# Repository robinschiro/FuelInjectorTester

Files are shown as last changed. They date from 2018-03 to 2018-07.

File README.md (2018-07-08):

# FuelInjectorTester
An Arduino-based device used to control fuel injectors for testing purposes.

# Background Information

- Injector injects onces per two turns of the engine

# Compiling the Code

- Get the Arduino IDE (https://www.arduino.cc/en/Main/OldSoftwareReleases)
- Unzip all dependencies (located in the 'Dependencies' folder) into the Arduino 'libraries' folder. The Arduino 'libraries' folder is located in the following locations (platform dependent):
	- (Windows) C:\Users\{User}\Documents\Arduino\libraries
	- (Unix) ~/sketchbook/libraries
- Open the 'FuelInjectorTester.ino' file using the Arduino IDE
- Click the button with a checkmark (top-left corner) to compile the code.

# Uploading Code to Arduino

# Requirements

- Support 4, 6, or 8 injectors
- LED lights that light up with fuel injectors
- Be able to adjust the following:
    - Number of injectors (4, 6 or 8)
    - Injection Time
    - RPM
    - Length of time the test will run
- Support different modes
    - Each mode should have configuration screen and running screen
    - Modes:
        - Testing
            - Injection Time: Range from 2 - 12 ms
            - RPM: range from 0 - 8000, increments of 100
        - Cleaning
            - Injection Time should range from 5 - 20 seconds, increments of 5
            - RPM: Range from 1 - 200 (use knob), increments of 1

# Problems
- If printing to LCD screen every frame, digital output to pins other than 13 does not work.
    - Possible Solution: Only drive the fuel injectors when in DRIVE_INJECTORS mode. In this mode, the UI is not updated. After exiting this mode, the UI will become responsive again.

# Express PCB Plus Grid Layout:
Grid: 2.5 mm
Snap: 0.25 mm

# Open questions
- Does simulating the firing order really matter?
	- Downside: Requires extra logic in the code

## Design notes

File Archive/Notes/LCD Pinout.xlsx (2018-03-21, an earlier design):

 | r5(sclk) | r3(d/c) | r1(sce) | vcc
red | yellow | blue | gray | black
brown | orange | green | violet | white
 | led | r4(dn) | r2(rst) | gnd

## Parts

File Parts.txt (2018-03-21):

Arduino Parts for Fuel Injector Project:

Vetco Electronics
15 day return policy

- New Arduino
- 2x Stackable header pins
    - 10 Pin Stacking Headers for Arduino (SKU: VUPN6552)
- Maybe a new shield that better fits my transistors
    - Need connections from the digital I/O pins to the shield holes
- Maybe a solution for my cable problem?
- Maybe a perf board?

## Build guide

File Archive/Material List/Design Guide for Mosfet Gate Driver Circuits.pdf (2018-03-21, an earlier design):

## Design And Application Guide For High Speed MOSFET Gate Drive Circuits

By Laszlo Balogh

ABSTRACT
The main purpose of this paper is to demonstrate a systematic approach to design high performance gate drive circuits for high speed switching applications. It is an informative collection of topics offering a “one-stop-shopping” to solve the most common design challenges. Thus it should be of interest to power electronics engineers at all levels of experience.
The most popular circuit solutions and their performance are analyzed, including the effect of parasitic components, transient and extreme operating conditions. The discussion builds from simple to more complex problems starting with an overview of MOSFET technology and switching operation. Design procedure for ground referenced and high side gate drive circuits, AC coupled and transformer isolated solutions are described in great details. A special chapter deals with the gate drive requirements of the MOSFETs in synchronous rectifier applications.
Several, step-by-step numerical design examples complement the paper.
INTRODUCTION
MOSFET – is an acronym for Metal Oxide
Semiconductor Field Effect Transistor and it is
the key component in high frequency, high efficiency switching applications across the electronics industry. It might be surprising, but FET technology was invented in 1930, some 20 years before the bipolar transistor. The first signal level FET transistors were built in the late 1950’s while power MOSFETs have been available from the mid 70’s. Today, millions of MOSFET transistors are integrated in modern electronic components, from microprocessors, through “discrete” power transistors.
The focus of this topic is the gate drive requirements of the power MOSFET in various switch mode power conversion applications. MOSFET TECHNOLOGY
The bipolar and the MOSFET transistors exploit the same operating principle. Fundamentally, both type of transistors are charge controlled devices which means that their output current is proportional to the charge established in the semiconductor by the control electrode. When these devices are used as switches, both must be driven from a low impedance source capable of sourcing and sinking sufficient current to provide for fast insertion and extraction of the controlling charge. From this point of view, the MOSFETs have to be driven just as “hard” during turn-on and turn-off as a bipolar transistor to achieve comparable switching speeds. Theoretically, the switching speeds of the bipolar and MOSFET devices are close to identical, determined by the time required for the charge carriers to travel across the semiconductor region. Typical values in power devices are approximately 20 to 200 picoseconds depending on the size of the device. The popularity and proliferation of MOSFET technology for digital and power applications is driven by two of their major advantages over the bipolar junction transistors. One of these benefits is the ease of use of the MOSFET devices in high frequency switching applications. The MOSFET transistors are simpler to drive because their control electrode is isolated from the current conducting silicon, therefore a continuous ON current is not required. Once the MOSFET transistors are turned-on, their drive current is practically zero. Also, the controlling charge and accordingly the storage time in the MOSFET transistors is greatly reduced. This basically eliminates the design trade-off between on state voltage drop – which is inversely proportional to excess control charge – and turn-off time. As a result, MOSFET technology promises to use much simpler and more efficient drive circuits with significant economic benefits compared to bipolar devices.
Furthermore, it is important to highlight especially for power applications, that MOSFETs have a resistive nature. The voltage drop across the drain source terminals of a MOSFET is a linear function of the current flowing in the semiconductor. This linear relationship is characterized by the RDS(on) of the MOSFET and known as the on-resistance. On-resistance is constant for a given gate-to-source voltage and temperature of the device. As opposed to the -2.2mV/°C temperature coefficient of a p-n junction, the MOSFETs exhibit a positive
temperature | coefficient | of | approximately
0.7%/°C to 1%/°C. This positive temperature coefficient of the MOSFET makes it an ideal candidate for parallel operation in higher power applications where using a single device would not be practical or possible. Due to the positive TC of the channel resistance, parallel connected MOSFETs tend to share the current evenly among themselves. This current sharing works automatically in MOSFETs since the positive TC acts as a slow negative feedback system. The device carrying a higher current will heat up more – don’t forget that the drain to source voltages are equal – and the higher temperature will increase its RDS(on) value. The increasing resistance will cause the current to decrease, therefore the temperature to drop. Eventually, an equilibrium is reached where the parallel connected devices carry similar current levels. Initial tolerance in RDS(on) values and different junction to ambient thermal resistances can cause significant – up to 30% – error in current distribution.
Device types
Almost all manufacturers have got their unique twist on how to manufacture the best power MOSFETs, but all of these devices on the market can be categorized into three basic device types. These are illustrated in Figure 1.

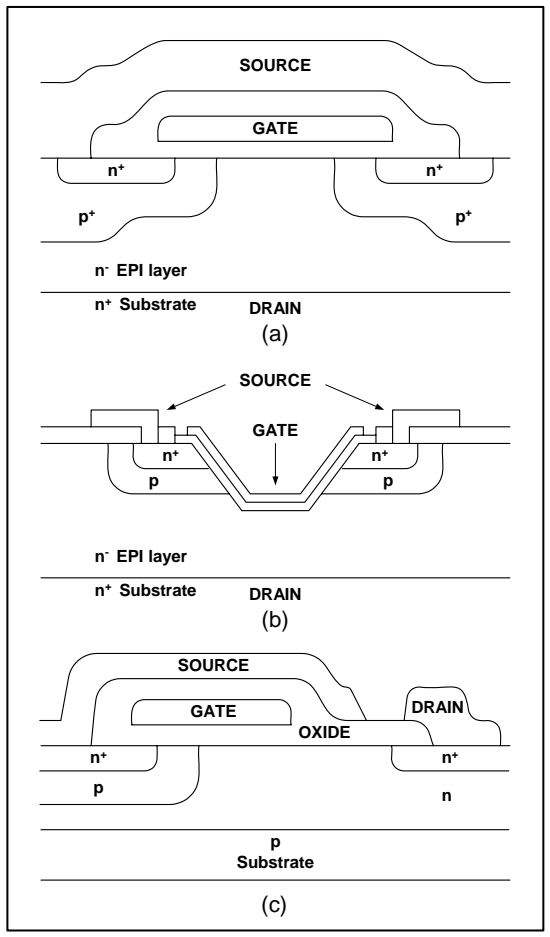
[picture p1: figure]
n⁺ Substrate; n⁻ EPI layer; GATE; SOURCE; DRAIN; Substrate; OXIDE

Figure 1. Power MOSFET device types
Double-diffused | MOS | transistors | were
introduced in the 1970’s for power applications and evolved continuously during the years. Using polycrystalline silicon gate structures and self-aligning processes, higher density integration and rapid reduction in capacitances became possible. The next significant advancement was offered by the V-groove or trench technology to further increase cell density in power MOSFET devices. The better performance and denser integration don’t come free however, as trench MOS devices are more difficult to manufacture.
The third device type to be mentioned here is the lateral power MOSFETs. This device type is constrained in voltage and current rating due to its inefficient utilization of the chip geometry. Nevertheless, they can provide significant benefits in low voltage applications, like in microprocessor power supplies or as synchronous rectifiers in isolated converters.

The lateral power MOSFETs have significantly lower capacitances, therefore they can switch much faster and they require much less gate drive power.
MOSFET Models
There are numerous models available to illustrate how the MOSFET works, nevertheless finding the right representation might be difficult. Most of the MOSFET manufacturers provide Spice and/or Saber models for their devices, but these models say very little about the application traps designers have to face in practice. They provide even fewer clues how to solve the most common design challenges.
A really useful MOSFET model which would describe all important properties of the device from an application point of view would be very complicated. On the other hand, very simple and meaningful models can be derived of the MOSFET transistor if we limit the applicability of the model to certain problem areas.
The first model in Figure 2 is based on the actual structure of the MOSFET device and can be used mainly for DC analysis. The MOSFET symbol in Figure 2a represents the channel resistance and the JFET corresponds to the resistance of the epitaxial layer. The length, thus the resistance of the epi layer is a function of the voltage rating of the device as high voltage MOSFETs require thicker epitaxial layer.
Figure 2b can be used very effectively to model the dv/dt induced breakdown characteristic of a MOSFET. It shows both main breakdown mechanisms, namely the dv/dt induced turn-on of the parasitic bipolar transistor - present in all power MOSFETs - and the dv/dt induced turn-on of the channel as a function of the gate
terminating | impedance. | Modern | power
MOSFETs are practically immune to dv/dt triggering of the parasitic npn transistor due to manufacturing improvements to reduce the resistance between the base and emitter regions. It must be mentioned also that the parasitic bipolar transistor plays another important role. Its base – collector junction is the famous body diode of the MOSFET.

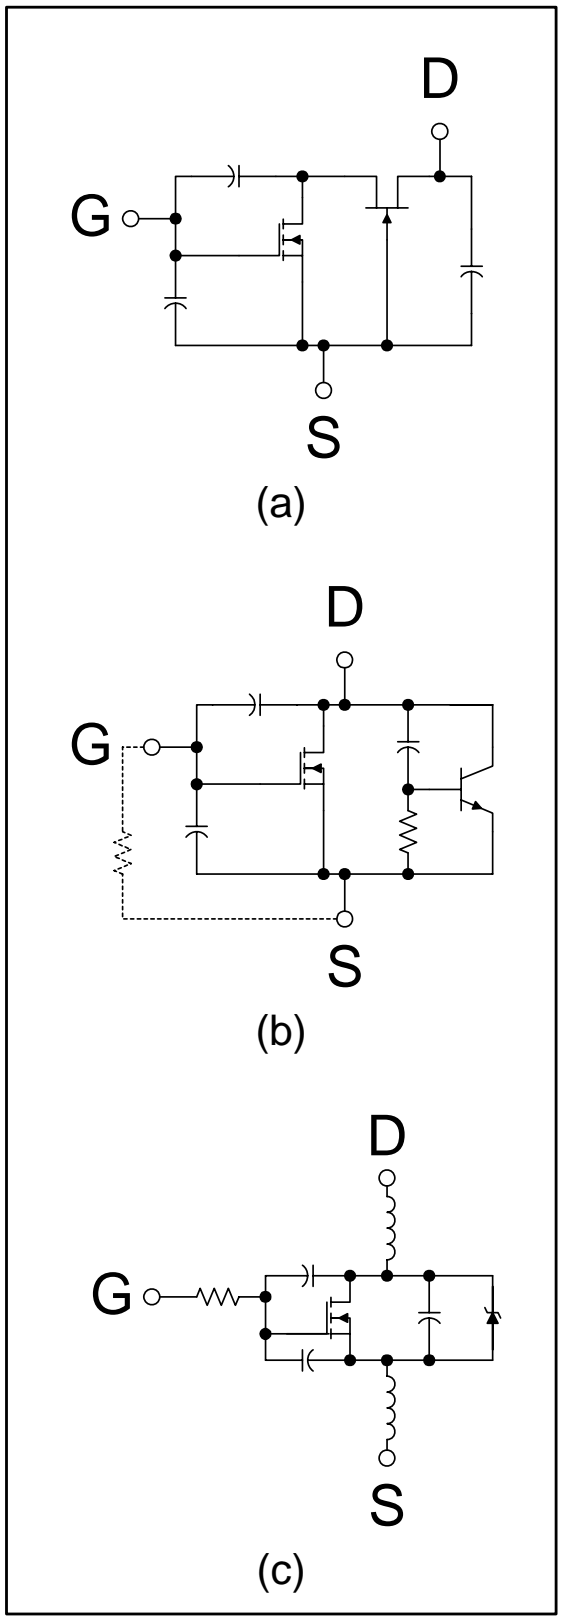
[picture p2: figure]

Figure 2. Power MOSFET models

Figure 2c is the switching model of the MOSFET. The most important parasitic components influencing switching performance are shown in this model. Their respective roles will be discussed in the next chapter which is dedicated to the switching procedure of the device.
MOSFET Critical Parameters
When switch mode operation of the MOSFET is considered, the goal is to switch between the lowest and highest resistance states of the device in the shortest possible time. Since the practical switching times of the MOSFETs (~10ns to 60ns) is at least two to three orders of magnitude longer than the theoretical switching time (~50ps to 200ps), it seems important to understand the discrepancy. Referring back to the MOSFET models in Figure 2, note that all models include three capacitors connected between the three terminals of the device. Ultimately, the switching performance of the MOSFET transistor is determined by how quickly the voltages can be changed across these capacitors.
Therefore, in high speed switching applications, the most important parameters are the parasitic capacitances of the device. Two of these
capacitors, the CGS | and CGD | capacitors
correspond to the actual geometry of the device while the CDS capacitor is the capacitance of the base collector diode of the parasitic bipolar transistor (body diode).
The CGS capacitor is formed by the overlap of the source and channel region by the gate electrode. Its value is defined by the actual geometry of the regions and stays constant (linear) under different operating conditions.
The CGD capacitor is the result of two effects. Part of it is the overlap of the JFET region and the gate electrode in addition to the capacitance of the depletion region which is non-linear. The equivalent CGD capacitance is a function of the drain source voltage of the device approximated by the following formula:

1 DS

GD,0
GD | 1 K | V
| C
C

+ ⋅ ≈

The CDS capacitor is also non-linear since it is the junction capacitance of the body diode. Its voltage dependence can be described as:

2 | DS

DS,0
DS | K | V

C
C ⋅ ≈

Unfortunately, non of the above mentioned capacitance values are defined directly in the transistor data sheets. Their values are given indirectly by the CISS, CRSS, and COSS capacitor values and must be calculated as:

DS | OSS | RSS
GS | ISS | RSS
GD | RSS
C | C | C
C | C | C
C | C
= | −
= | −

=

Further complication is caused by the CGD capacitor in switching applications because it is placed in the feedback path between the input and output of the device. Accordingly, its effective value in switching applications can be much larger depending on the drain source voltage of the MOSFET. This phenomenon is called the “Miller” effect and it can be expressed as:
( | ) CGD,eqv | 1 gfs RL | CGD = + ⋅ | ⋅

Since the CGD and CDS capacitors are voltage dependent, the data sheet numbers are valid only at the test conditions listed. The relevant average capacitances for a certain application have to be calculated based on the required charge to establish the actual voltage change across the capacitors. For most power MOSFETs the following approximations can be useful:

DS,off

DS,spec
OSS,ave | OSS,spec

DS,off

DS,spec
GD,ave | RSS,spec

V

V
C 2 C

V

V
C | 2 C
= ⋅ | ⋅
= ⋅ | ⋅

The next important parameter to mention is the gate mesh resistance, RG,I. This parasitic resistance describes the resistance associated by the gate signal distribution within the device. Its importance is very significant in high speed switching applications because it is in between the driver and the input capacitor of the device, directly impeding the switching times and the dv/dt immunity of the MOSFET. This effect is recognized in the industry, where real high speed devices like RF MOSFET transistors use metal gate electrodes instead of the higher resistance polysilicon gate mesh for gate signal distribution. The RG,I resistance is not specified in the data sheets, but in certain applications it can be a very important characteristic of the device. In the back of this paper, Appendix A4 shows a typical measurement setup to determine the internal gate resistor value with an impedance bridge. Obviously, the gate threshold voltage is also a critical characteristic. It is important to note that the data sheet VTH value is defined at 25°C and at a very low current, typically at 250μA. Therefore, it is not equal to the Miller plateau region of the commonly known gate switching waveform. Another rarely mentioned fact about VTH is its approximately –7mV/°C temperature coefficient. It has particular significance in gate drive circuits designed for logic level MOSFET where VTH is already low under the usual test conditions. Since MOSFETs usually operate at elevated temperatures, proper gate drive design must account for the lower VTH when turn-off time, and dv/dt immunity is calculated as shown in Appendix A and F.
The transconductance of the MOSFET is its small signal gain in the linear region of its operation. It is important to point out that every time the MOSFET is turned-on or turned-off, it must go through its linear operating mode where the current is determined by the gate-to-source voltage. The transconductance, gfs, is the small signal relationship between drain current and gate-to-source voltage:

GS

D
fs dV

dI
g =

Accordingly, the maximum current of the MOSFET in the linear region is given by:
( | ) D | VGS | Vth | gfs I = | − | ⋅

Rearranging this equation for VGS yields the approximate value of the Miller plateau as a function of the drain current.

fs

D
GS,Miller th
g

I V = V +

Other important parameters like the source inductance (LS) and drain inductance (LD) exhibit significant restrictions in switching performance. Typical LS and LD values are listed in the data sheets, and they are mainly dependant on the package type of the transistor. Their effects can be investigated together with the external parasitic components usually associated with layout and with accompanying external circuit elements like leakage inductance, a current sense resistor, etc.
For completeness, the external series gate resistor and the MOSFET driver’s output impedance must be mentioned as determining factors in high performance gate drive designs as they have a profound effect on switching speeds and consequently on switching losses.
SWITCHING APPLICATIONS
Now, that all the players are identified, let’s investigate the actual switching behavior of the MOSFET transistors. To gain a better understanding of the fundamental procedure, the parasitic inductances of the circuit will be neglected. Later their respective effects on the basic operation will be analyzed individually. Furthermore, the following descriptions relate to clamped inductive switching because most MOSFET transistors and high speed gate drive circuits used in switch mode power supplies work

Figure 3. Simplified clamped inductive switching model

The simplest model of clamped inductive switching is shown in Figure 3, where the DC current source represents the inductor. Its current can be considered constant during the short switching interval. The diode provides a path for the current during the off time of the MOSFET and clamps the drain terminal of the device to the output voltage symbolized by the battery. Turn-On procedure
The turn-on event of the MOSFET transistor can be divided into four intervals as depicted in Figure 4.

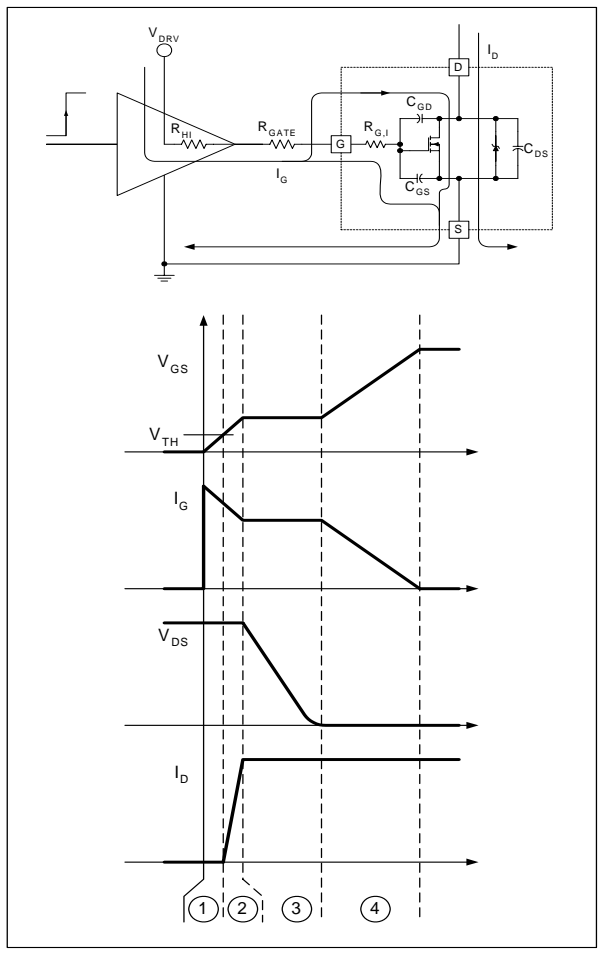
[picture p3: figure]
V DRV; RHI; RGATE; CGS; CDS; VGS; VTH

Figure 4. MOSFET turn-on time intervals In the first step the input capacitance of the device is charged from 0V to VTH. During this interval most of the gate current is charging the CGS capacitor. A small current is flowing through the CGD capacitor too. As the voltage increases at the gate terminal and the CGD capacitor’s voltage has to be slightly reduced.

This period is called the turn-on delay, because both the drain current and the drain voltage of the device remain unchanged.
Once the gate is charged to the threshold level, the MOSFET is ready to carry current. In the second interval the gate is rising from VTH to the Miller plateau level, VGS,Miller. This is the linear operation of the device when current is proportional to the gate voltage. On the gate side, current is flowing into the CGS and CGD capacitors just like in the first time interval and the VGS voltage is increasing. On the output side of the device, the drain current is increasing, while the drain-to-source voltage stays at the previous level (VDS,OFF). This can be understood looking at the schematic in Figure 3. Until all the current is transferred into the MOSFET and the diode is turned-off completely to be able to block reverse voltage across its pn junction, the drain voltage must stay at the output voltage level. Entering into the third period of the turn-on procedure the gate is already charged to the sufficient voltage (VGS,Miller) to carry the entire load current and the rectifier diode is turned off. That now allows the drain voltage to fall. While the drain voltage falls across the device, the gate-to-source voltage stays steady. This is the Miller plateau region in the gate voltage waveform. All the gate current available from the driver is diverted to discharge the CGD capacitor to facilitate the rapid voltage change across the drain-to-source terminals. The drain current of the device stays constant since it is now limited by the external circuitry, i.e. the DC current source.
The last step of the turn-on is to fully enhance the conducting channel of the MOSFET by applying a higher gate drive voltage. The final amplitude of VGS determines the ultimate on-resistance of the device during its on-time. Therefore, in this fourth interval, VGS is increased from VGS,Miller to its final value, VDRV. This is accomplished by charging the CGS and CGD capacitors, thus gate current is now split between the two components. While these capacitors are being charged, the drain current is still constant, and the drain-to-source voltage is slightly decreasing as the on-resistance of the device is being reduced.

Turn-Off procedure
The description of the turn-off procedure for the MOSFET transistor is basically back tracking the turn-on steps from the previous section. Start with VGS being equal to VDRV and the current in the device is the full load current represented by IDC in Figure 3. The drain-to-source voltage is being defined by IDC and the RDS(on) of the MOSFET. The four turn-off steps are shown in Figure 5. for completeness.

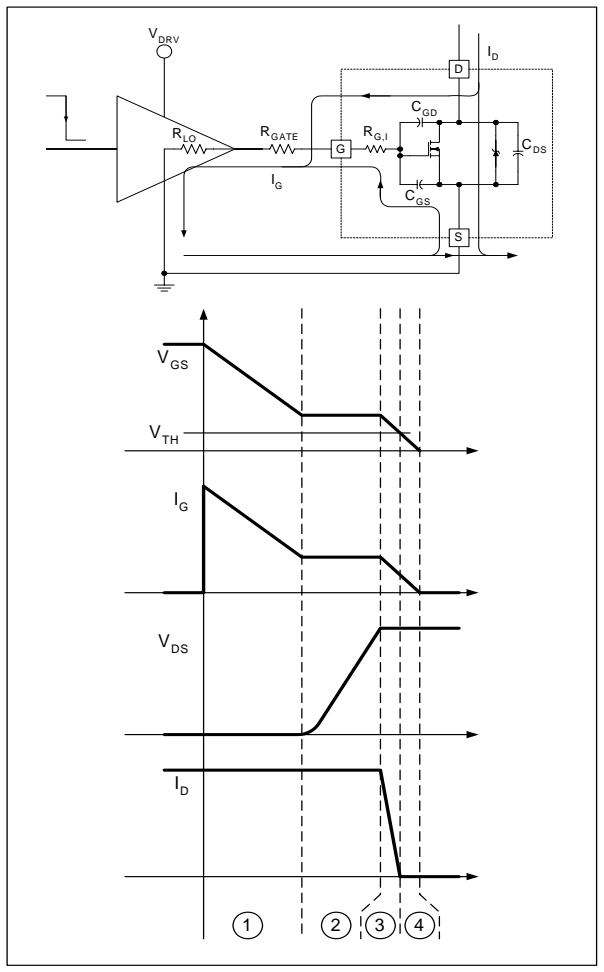
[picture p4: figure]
VDRV; RLO; RGATE; CGD; CGS; CDS; VDS; VGS; VTH

Figure 5. MOSFET turn-off time intervals The first time interval is the turn-off delay which is required to discharge the CISS capacitance from its initial value to the Miller plateau level. During this time the gate current is supplied by the CISS capacitor itself and it is flowing through the CGS and CGD capacitors of the MOSFET. The drain voltage of the device is slightly increasing as the overdrive voltage is diminishing. The current in the drain is unchanged.

In the second period, the drain-to-source voltage of the MOSFET rises from ID⋅RDS(on) to the final VDS(off) level, where it is clamped to the output voltage by the rectifier diode according to the simplified schematic of Figure 3. During this time period – which corresponds to the Miller plateau in the gate voltage waveform - the gate current is strictly the charging current of the CGD capacitor because the gate-to-source voltage is constant. This current is provided by the bypass capacitor of the power stage and it is subtracted from the drain current. The total drain current still equals the load current, i.e. the inductor current represented by the DC current source in Figure 3.
The beginning of the third time interval is signified by the turn-on of the diode, thus providing an alternative route to the load current. The gate voltage resumes falling from VGS,Miller to VTH. The majority of the gate current is coming out of the CGS capacitor, because the CGD capacitor is virtually fully charged from the previous time interval. The MOSFET is in linear operation and the declining gate-to-source voltage causes the drain current to decrease and reach near zero by the end of this interval. Meanwhile the drain voltage is steady at VDS(off) due to the forward biased rectifier diode.
The last step of the turn-off procedure is to fully discharge the input capacitors of the device. VGS is further reduced until it reaches 0V. The bigger portion of the gate current, similarly to the third turn-off time interval, supplied by the CGS capacitor. The drain current and the drain voltage in the device are unchanged.
Summarizing the results, it can be concluded that the MOSFET transistor can be switched between its highest and lowest impedance states (either turn-on or turn-off) in four time intervals. The lengths of all four time intervals are a function of the parasitic capacitance values, the required voltage change across them and the available gate drive current. This emphasizes the importance of the proper component selection and optimum gate drive design for high speed, high frequency switching applications.

Characteristic numbers for turn-on, turn-off delays, rise and fall times of the MOSFET switching waveforms are listed in the transistor data sheets. Unfortunately, these numbers correspond to the specific test conditions and to resistive load, making the comparison of different
manufacturers’ | products | difficult. | Also,
switching performance in practical applications with clamped inductive load is significantly different from the numbers given in the data sheets.
Power losses
The switching action in the MOSFET transistor in power applications will result in some unavoidable losses, which can be divided into two categories.
The simpler of the two loss mechanisms is the gate drive loss of the device. As described before, turning-on or off the MOSFET involves charging or discharging the CISS capacitor. When the voltage across a capacitor is changing, a certain amount of charge has to be transferred. The amount of charge required to change the gate voltage between 0V and the actual gate drive voltage VDRV, is characterized by the typical gate charge vs. gate-to-source voltage curve in the MOSFET datasheet. An example is shown in

# Figure 6. Vgs, Gate⁻to⁻Source Voltage ⁽V⁾

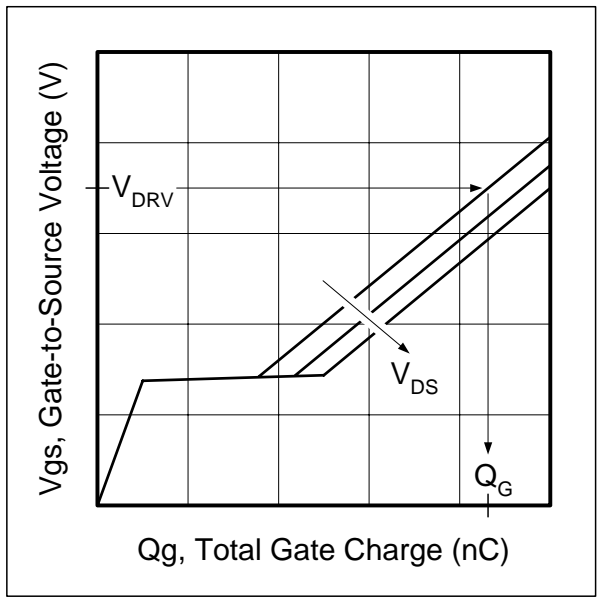
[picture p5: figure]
Qg, Total Gate Charge (nC); VDS; VDRV

Figure 6. Typical gate charge vs. gate-to-source voltage

This graph gives a relatively accurate worst case estimate of the gate charge as a function of the gate drive voltage. The parameter used to generate the individual curves is the drain-to-source off state voltage of the device. VDS(off) influences the Miller charge – the area below the flat portion of the curves – thus also, the total gate charge required in a switching cycle. Once the total gate charge is obtained from Figure 6, the gate charge losses can be calculated as:

GATE | DRV | G | DRV P | = V | ⋅Q ⋅f
where VDRV is the amplitude of the gate drive waveform and fDRV is the gate drive frequency – which is in most cases equal to the switching frequency. It is interesting to notice that the QG⋅fDRV term in the previous equation gives the average bias current required to drive the gate. The power lost to drive the gate of the MOSFET transistor is dissipated in the gate drive circuitry. Referring back to Figures 4 and 5, the dissipating components can be identified as the combination of the series ohmic impedances in the gate drive path. In every switching cycle the required gate charge has to pass through the driver output impedances, the external gate resistor, and the internal gate mesh resistance. As it turns out, the power dissipation is independent of how quickly the charge is delivered through the resistors. Using the resistor designators from Figures 4 and 5, the driver power dissipation can be expressed as:
DRV | DRV,ON | DRV,OFF
LO | GATE | G,I
LO | DRV | G | DRV
DRV,OFF
HI | GATE | | G,I
HI | DRV | G | DRV
DRV,ON
P | P | P
R | R | R
R | V | Q f
2

1 P

R | R | R
R | V | Q f
2

1 P

= | +
+ | +
⋅ | ⋅ | ⋅ = ⋅
+ | +
⋅ | ⋅ | ⋅ = ⋅

In the above equations, the gate drive circuit is represented by a resistive output impedance and this assumption is valid for MOS based gate drivers. When bipolar transistors are utilized in the gate drive circuit, the output impedance becomes non-linear and the equations do not yield the correct answers. It is safe to assume that with low value gate resistors (<5Ω) most gate drive losses are dissipated in the driver. If RGATE is sufficiently large to limit IG below the output current capability of the bipolar driver, the majority of the gate drive power loss is then dissipated in RGATE.
In addition to the gate drive power loss, the transistors accrue switching losses in the traditional sense due to high current and high
voltage | being | present | in | the | device
simultaneously for a short period. In order to ensure the least amount of switching losses, the duration of this time interval must be minimized. Looking at the turn-on and turn-off procedures of the MOSFET, this condition is limited to intervals 2 and 3 of the switching transitions in both turn-on and turn-off operation. These time intervals correspond to the linear operation of the device when the gate voltage is between VTH and VGS,Miller, causing changes in the current of the device and to the Miller plateau region when the drain voltage goes through its switching transition.
This is a very important realization to properly design high speed gate drive circuits. It highlights the fact that the most important characteristic of the gate driver is its source-sink current capability around the Miller plateau voltage level. Peak current capability, which is measured at full VDRV across the driver’s output impedance, has very little relevance to the actual switching performance of the MOSFET. What really determines the switching times of the device is the gate drive current capability when the gate-to-source voltage, i.e. the output of the driver is at ~5V (~2.5V for logic level MOSFETs).
A crude estimate of the MOSFET switching losses can be calculated using simplified linear approximations of the gate drive current, drain current and drain voltage waveforms during periods 2 and 3 of the switching transitions. First the gate drive currents must be determined for the second and third time intervals respectively:
( | )
HI | GATE | G.I
DRV | GS,Miller
G3
HI | GATE | G.I
DRV | GS,Miller | TH
G2
R | R | R
V | V
I
R | R | R
V | 0.5 V | V
I

+ +

− =

+ | +
− | ⋅ | + =

Assuming that IG2 charges the input capacitor of the device from VTH to VGS,Miller and IG3 is the discharge current of the CRSS capacitor while the drain voltage changes from VDS(off) to 0V, the approximate switching times are given as:

G3

DS,off
RSS

G2

GS,Miller TH
ISS

I

V
t3 C

I

V V
t2 C
= | ⋅
− = | ⋅

During t2 the drain voltage is VDS(off) and the current is ramping from 0A to the load current, IL while in t3 time interval the drain voltage is falling from VDS(off) to near 0V. Again, using linear approximations of the waveforms, the power loss components for the respective time intervals can be estimated:

L

DS,off

L
DS,off

I
2

V
T

t3 P3

2

I V
T

t2 P2

= ⋅ | ⋅
= ⋅ | ⋅

where T is the switching period. The total switching loss is the sum of the two loss components, which yields the following simplifed expression:

Even though the switching transitions are well understood, calculating the exact switching losses is almost impossible. The reason is the effect of the parasitic inductive components which will significantly alter the current and voltage waveforms, as well as the switching times during the switching procedures. Taking into account the effect of the different source and drain inductances of a real circuit would result in second order differential equations to describe the actual waveforms of the circuit. Since the variables, including gate threshold voltage, MOSFET capacitor values, driver output impedances, etc. have a very wide tolerance, the above described linear approximation seems to be a reasonable enough compromise to estimate switching losses in the MOSFET.
Effects of parasitic components
The most profound effect on switching performance is exhibited by the source inductance. There are two sources for parasitic source inductance in a typical circuit, the source

T

t2 t3
2
V | I
P | DS(off) | L
SW

+ ⋅ ⋅ =

bond wire neatly integrated into the MOSFET package and the printed circuit board wiring inductance between the source lead and the common ground. This is usually referenced as the negative electrode of the high frequency filter capacitor around the power stage and the bypass capacitor of the gate driver. Current sense resistors in series with the source can add additional inductance to the previous two components.
There are two mechanisms in the switching procedure which involve the source inductor. At the beginning of the switching transitions the gate current is increasing very rapidly as illustrated in Figures 4 and 5. This current must flow through the source inductance and will be slowed down based on the inductor value. Consequently, the time required to charge/discharge the input capacitance of the MOSFET gets longer, mainly influencing the turn-on and turn-off delays (step 1). Furthermore, the source inductor and the CISS capacitor form a resonant circuit as shown in Figure 7.

VDRV

RG

LS

CISS

Figure 7. Gate drive resonant circuit components The resonant circuit is exited by the steep edges of the gate drive voltage waveform and it is the fundamental reason for the oscillatory spikes observed in most gate drive circuits. Fortunately, the otherwise very high Q resonance between CISS and LS is damped or can be damped by the series resistive components of the loop which include the driver output impedance, the external gate resistor, and the internal gate mesh resistor. The only user adjustable value, RGATE, can be calculated for optimum performance by:

( | ) DRV | G,I

ISS

S
GATE,OPT | R | R
C
L R | = 2⋅ | − | +

Smaller resistor values will result an overshoot in the gate drive voltage waveform, but also result in faster turn-on speed. Higher resistor values will underdamp the oscillation and extend the switching times without offering any benefit for the gate drive design.
The second effect of the source inductance is a negative feedback whenever the drain current of the device is changing rapidly. This effect is present in the second time interval of the turn-on and in the third time interval of the turn-off procedure. During these periods the gate voltage is between VTH and VGS,Miller, and the gate current is defined by the voltage across the drive impedance, VDRV-VGS. In order to increase the drain current quickly, significant voltage has to be applied across the source inductance. This voltage reduces the available voltage across the drive impedance, thus reduces the rate of change in the gate drive voltage which will result in a lower di/dt of the drain current. The lower di/dt requires less voltage across the source inductance. A delicate balance of gate current and drain di/dt is established through the negative feedback by the source inductor.
The other parasitic inductance of the switching network is the drain inductance which is again composed of several components. They are the packaging inductance inside the transistor package, all the inductances associated with interconnection and the leakage inductance of a transformer in isolated power supplies. Their effect can be lumped together since they are in series with each other. They act as a turn-on snubber for the MOSFET. During turn-on they limit the di/dt of the drain current and reduce the drain-to-source voltage across the device by the factor of LD⋅di/dt. In fact, LD can reduce the turn-on switching losses significantly. While higher LD values seem beneficial at turn-on, they cause considerable problems at turn-off when the drain current must ramp down quickly. To support the rapid reduction in drain current due to the turn-off of the MOSFET, a voltage in the opposite direction with respect to turn-on must be across LD. This voltage is above the theoretical VDS(off) level, producing an overshoot in the drain-to-source voltage and an increase in turn-off switching losses.

Accurate mathematical analysis of the complete switching transitions including the effects of parasitic inductances are available in the literature but points beyond the scope of this paper.
GROUND REFERENCED GATE
DRIVE

PWM Direct drive
In power supply applications, the simplest way of driving the gate of the main switching transistor is to utilize the gate drive output of the PWM controller as shown in Figure 8.

Figure 8. Direct gate drive circuit
The most difficult task in direct gate drives is to optimize the circuit layout. As indicated in Figure 8, there might be considerable distance between the PWM controller and the MOSFET. This distance introduces a parasitic inductance due to the loop formed by the gate drive and ground return traces which can slow down the switching speed and can cause ringing in the gate drive waveform. Even with a ground plane, the inductance can not be completely eliminated since the ground plane provides a low inductance path for the ground return current only. To reduce the inductance linked to the gate drive connection, a wider PCB trace is desirable. Another problem in direct gate drive is the limited drive current capability of the PWM controllers. Very few integrated circuits offer more than 1A peak gate drive capability. This will limit the maximum die size which can be driven at a reasonable speed by the controller.

Another limiting factor for MOSFET die size with direct gate drive is the power dissipation of the driver within the controller. An external gate resistor can mitigate this problem as discussed before. When direct gate drive is absolutely necessary for space and/or cost savings, special considerations are required to provide appropriate bypassing for the controller. The high current spikes driving the gate of the MOSFET can disrupt the sensitive analog circuitry inside the PWM controller. As MOSFET die size increases, so too does gate charge required. The selection of the proper bypass capacitor calls for a little bit more scientific approach than picking the usual 0.1μF or 1μF bypass capacitor.

Sizing the bypass capacitor
In this chapter the calculation of the MOSFET gate driver’s bypass capacitor is demonstrated. This capacitor is the same as the PWM controller’s bypass capacitor in direct gate drive application because that is the capacitor which provides the gate drive current at turn-on. In case of a separate driver circuit, whether a gate drive IC or discrete solution, this capacitor must be placed close, preferably directly across the bias and ground connection of the driver.
There are two current components to consider. One is the quiescent current which can change by a 10x factor based on the input state of some integrated drivers. This itself will cause a duty cycle dependent ripple across the bypass capacitor which can be calculated as:
DRV | DRV
| Q,HI | MAX
Q | C | f
| I | D
ΔV | ⋅

⋅ =

where it is assumed that the driver’s quiescent current is higher when its input is driven high. The other ripple component is the gate current. Although the actual current amplitude is not know in most cases, the voltage ripple across the bypass capacitor can be determined based on the value of the gate charge. At turn-on, this charge is taken out of the bypass capacitor and transferred to the MOSFET input capacitor. Accordingly the ripple is given by:

DRV

G
QG C

Q ΔV =

Using the principle of superposition and solving the equations for CDRV, the bypass capacitor value for a tolerable ripple voltage (ΔV) can be found:

ΔV

Q f

D I

C

G
DRV

MAX
Q,HI

DRV

⋅ +
=

where IQ,HI is the quiescent current of the driver when its input is driven high, DMAX is the maximum duty cycle of the driver while the input can stay high, fDRV is the operating frequency of the driver, and QG is the total gate charge based on the amplitude of the gate drive and drain-to-source off state voltages.
Driver protection
Another must-do with direct drive and with gate drive ICs using bipolar output stage is to provide suitable protection for the output bipolar transistors against reverse currents. As indicated in the simplified diagram in Figure 9, the output stage of the integrated bipolar drivers is built from npn transistors due to their more efficient

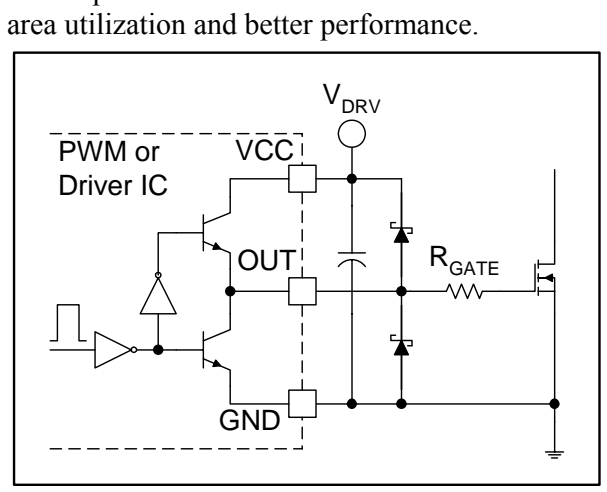
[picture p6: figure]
area utilization and better performance.; RGATE; VCC; OUT; GND; VDRV; PWM or Driver IC

Figure 9. Gate drive with integrated bipolar transistors
The npn transistors can handle currents in one direction only. The high side npn can source but can not sink current while the low side is exactly the opposite. Unavoidable oscillations between the source inductor and the input capacitor of the MOSFET during turn-on and turn-off necessitate that current should be able to flow in both directions at the output of the driver. To provide a path for reverse currents, low forward voltage drop Schottky diodes are generally needed to protect the outputs. The diodes must be placed very close to the output pin and to the bypass capacitor of the driver. It is important to point out also, that the diodes protect the driver only, they are not clamping the gate-to-source voltage against excessive ringing especially with direct drive where the control IC might be far away from the gate-source terminals of the MOSFET. Bipolar totem-pole driver
One of the most popular and cost effective drive circuit for driving MOSFETs is a bipolar, non-inverting totem-pole driver as shown in Figure

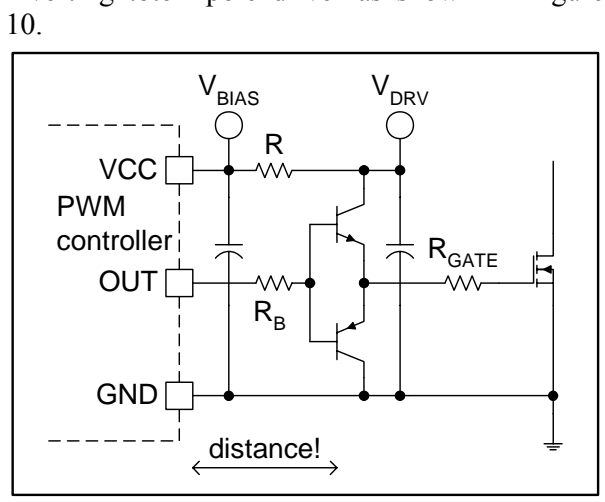
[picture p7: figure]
RGATE; VCC; OUT; GND; VBIAS; VDRV; distance!; PWM controller

Figure 10. Bipolar totem-pole MOSFET driver Like all external drivers, this circuit handles the current spikes and power losses making the operating conditions for the PWM controller more favorable. Of course, they can be and should be placed right next to the power MOSFET they are driving. That way the high current transients of driving the gate are localized in a very small loop area, reducing the value of parasitic inductances. Even though the driver is built from discrete components, it needs its own bypass capacitor placed across the collectors of the upper npn and the lower pnp transistors. Ideally there is a smoothing resistor or inductor between the bypass capacitor of the driver and the bypass capacitor of the PWM controller for increased noise immunity. The RGATE resistor of Figure 10 is optional and RB can be sized to provide the required gate impedance based on the large signal beta of the driver transistors.

An interesting property of the bipolar totem-pole driver that the two base-emitter junctions protect
each | other | against | reverse | breakdown.
Furthermore, assuming that the loop area is really small and RGATE is negligible, they can clamp the gate voltage between VBIAS+VBE and GND-VBE using the base-emitter diodes of the transistors. Another benefit of this solution, based on the same clamp mechanism, is that the npn-pnp totem-pole driver does not require any Schottky diode for reverse current protection.
MOSFET totem-pole driver
The MOSFET equivalent of the bipolar totem-pole driver is pictured in Figure 11. All the benefits mentioned about the bipolar totem-pole

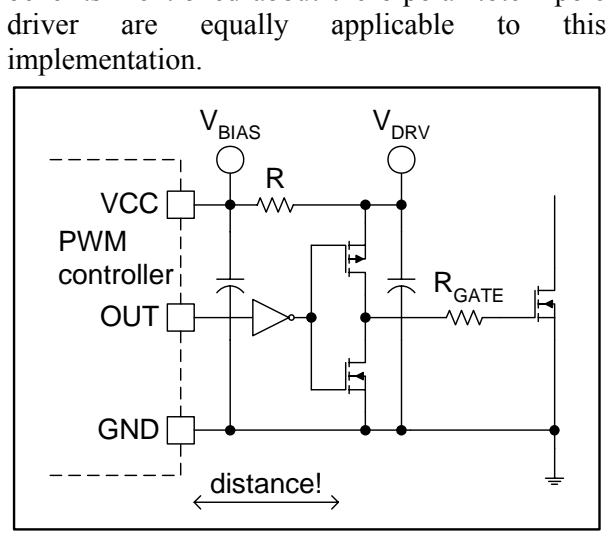
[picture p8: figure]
driver; are; equally; applicable; this; implementation.; RGATE; VCC; OUT; GND; VBIAS; VDRV; distance!; PWM controller

Figure 11. MOSFET based totem-pole driver Unfortunately, this circuit has several drawbacks compared to the bipolar version which explain that it is very rarely implemented discretely. The circuit of Figure 11 is an inverting driver, therefore the PWM output signal must be inverted. In addition, the suitable MOSFET transistors are more expensive than the bipolar ones and they will have a large shoot through current when their common gate voltage is in transition. This problem can be circumvented by additional logic or timing components which
technique | is | extensively | used | in | IC
implementations.

Speed enhancement circuits
When speed enhancement circuits are mentioned designers exclusively consider circuits which speed-up the turn-off process of the MOSFET. The reason is that the turn-on speed is usually limited by the turn-off, or reverse recovery speed of the rectifier component in the power supply. As discussed with respect to the inductive clamped model in Figure 3, the turn-on of the MOSFET coincides with the turn-off of the rectifier diode. Therefore, the fastest switching action is determined by the reverse recovery characteristic of the diode, not by the strength of the gate drive circuit. In an optimum design the gate drive speed at turn-on is matched to the diode switching characteristic. Considering also that the Miller region is closer to GND than to the final gate drive voltage VDRV, a higher voltage can be applied across the driver output impedance and the gate resistor. Usually the obtained turn-on speed is sufficient to drive the MOSFET.
The situation is vastly different at turn-off. In theory, the turn-off speed of the MOSFET depends only on the gate drive circuit. A higher current turn-off circuit can discharge the input capacitors quicker, providing shorter switching times and consequently lower switching losses. The higher discharge current can be achieved by a lower output impedance MOSFET driver and/or a negative turn-off voltage in case of the common N-channel device. While faster switching can potentially lower the switching losses, the turn-off speed-up circuits increase the ringing in the waveforms due to the higher turn-off di/dt and dv/dt of the MOSFET. This is something to consider in selecting the proper voltage rating and EMI containment for the power device.
Turn-off diode
The following examples of turn-off circuits are demonstrated on simple ground referenced gate drive circuits, but are equally applicable to other implementations discussed later in the paper. The simplest technique is the anti-parallel diode, as shown in Figure 12.

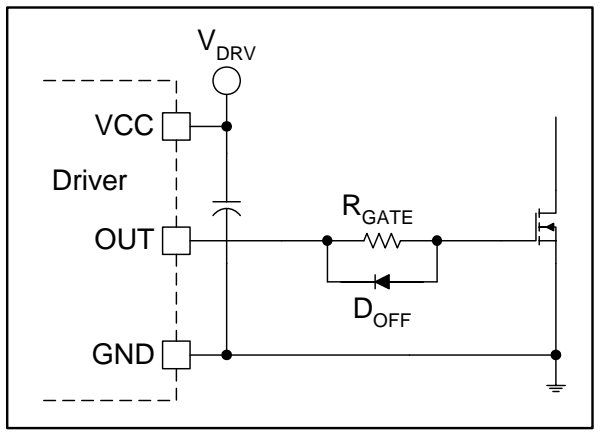
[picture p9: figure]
RGATE; VCC; OUT; GND; VDRV; Driver; DOFF

Figure 12. Simple turn-off speed enhancement circuit
In this circuit RGATE allows adjustment of the MOSFET turn-on speed. During turn-off the anti-parallel diode shunts out the resistor. DOFF works only when the gate current is higher than:

GATE

D,FWD
G R

V
I >

typically around 150mA using a 1N4148 and around 300mA with a BAS40 Schottky anti-parallel diode. Consequently, as the gate-to-source voltage approaches 0V the diode helps less and less. As a result, this circuit will provide a significant reduction in turn-off delay time, but only incremental improvement on switching times and dv/dt immunity. Another disadvantage is that the gate turn-off current still must flow through the driver’s output impedance.
PNP turn-off circuit
Undoubtedly the most popular arrangement for fast turn-off is the local pnp turn-off circuit of Figure 13. With the help of QOFF, the gate and the source are shorted locally at the MOSFET terminals during turn-off. RGATE limits the turn-on speed, and DON provides the path for the turn-on current. Also, DON protects the base-emitter junction of QOFF against reverse breakdown at the beginning of the turn-on procedure.
The most important advantage of this solution is that the high peak discharge current of the MOSFET input capacitance is confined in the smallest possible loop between the gate, source and collector, emitter connections of the two transistors.

Figure 13. Local pnp turn-off circuit
The turn-off current does not go back to the driver, it does not cause ground bounce problems and the power dissipation of the driver is reduced by a factor of two. The turn-off transistor shunts out the gate drive loop inductance, the potential current sense resistor, and the output impedance of the driver. Furthermore, QOFF never saturates which is important to be able to turn it on and off quickly. Taking a closer look at the circuit reveals that this solution is a simplified bipolar totem-pole driver, where the npn pull-up transistor is replaced by a diode. Similarly to the totem-pole driver, the MOSFET gate is clamped by the turn-off circuit between GND-0.7V and VDRV+0.7V approximately, eliminating the risk of excessive voltage stress at the gate. The only known shortcoming of the circuit is that it can not pull the gate all the way to 0V because of the voltage drop across the base-emitter junction of
QOFF.
NPN turn-off circuit
The next circuit to examine is the local npn turn-off circuit, illustrated in Figure 14. Similarly to the pnp solution, the gate discharge current is well localized. The npn transistor holds the gate closer to GND than its pnp counterpart. Also, this
implementation | provides | a | self biasing
mechanism to keep the MOSFET off during power up.
Unfortunately, this circuit has some significant drawbacks. The npn turn-off transistor, QOFF is an inverting stage, it requires an inverted PWM signal provided by QINV.

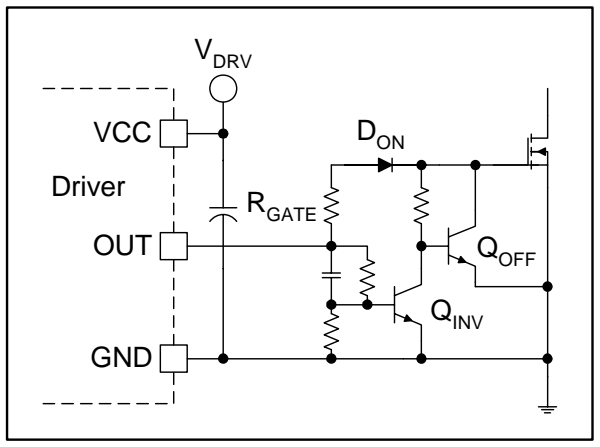
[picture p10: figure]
RGATE; VCC; OUT; GND; VDRV; Driver; DON; QOFF; QINV

Figure 14. Local npn self biasing turn-off circuit The inverter draws current from the driver during the on time of the MOSFET, lowering the efficiency of the circuit. Furthermore, QINV saturates during the on-time which can prolong turn-off delay in the gate drive.
NMOS turn-off circuit
An improved, lower parts count implementation of this principle is offered in Figure 15, using a dual driver to provide the inverted PWM signal for a small N-channel discharge transistor.

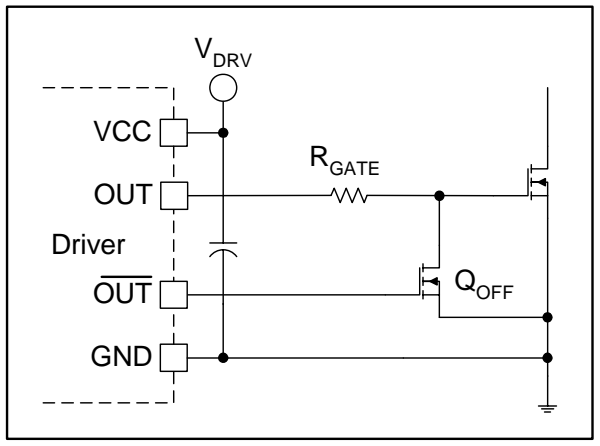
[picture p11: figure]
RGATE; VCC; OUT; GND; VDRV; Driver; QOFF

Figure 15. Improved N-channel MOS based turn-off circuit
This circuit offers very fast switching and complete discharge of the MOSFET gate to 0V. RGATE sets the turn-on speed like before, but is also utilized to prevent any shoot through currents between the two outputs of the driver in case of imperfect timing of the drive signals. Another important fact to consider is that the COSS capacitance of QOFF is connected in parallel to the CISS capacitance of the main power MOSFET. This will increase the effective “Total Gate Charge” the driver has to provide. Also to consider, the gate of the main MOSFET is floating before the outputs of the driver IC becomes intelligent during power up.
dv/dt protection
There are two situations when the MOSFET has to be protected against dv/dt triggered turn-on. One is during power up where protection can usually be provided by a resistor between the gate and source terminals of the device. The pull down resistor value depends on the worst case dv/dt of the power rail during power up according to:
GD | TURN ON

TH
GS | dv

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
⎛ < ⋅

In this calculation the biggest challenge is to find the highest dv/dt which can occur during power up and provide sufficient protection for that particular dv/dt.
The second situation is in normal operation when turn-off dv/dt is forced across the drain-to-source terminals of the power switch while it is off. This situation is more common than one may originally anticipate. All synchronous rectifier switches are operated in this mode as will be discussed later. Most resonant and soft switching converters can force a dv/dt across the main switch right after its turn-off instance, driven by the resonant components of the power stage. Since these dv/dt’s are significantly higher than during power up and VTH is usually lower due to the higher operating junction temperature, protection must be provided by the low output impedance of the gate drive circuit.
The first task is to determine the maximum dv/dt which can occur under worst case conditions. The next step in evaluating the suitability of a particular device to the application is to calculate its natural dv/dt limit, imposed by the internal gate resistance and the CGD capacitance of the MOSFET. Assuming ideal (zero Ohm) external drive impedance the natural dv/dt limit is:
( | )
G,I | GD
TH | J
LIMIT | R | C
V | 0.007 T 25
dt

dv
⋅
− | ⋅ | − =

where VTH is the gate threshold at 25°C, -0.007 is the temperature coefficient of VTH, RG,I is the internal gate mesh resistance and CGD is the gate-to-drain capacitor. If the natural dv/dt limit of the MOSFET is lower than the maximum dv/dt of the resonant circuit, either a different MOSFET or a negative gate bias voltage must be considered. If the result is favorable for the device, the maximum gate drive impedance can be calculated by rearranging and solving the previous equation according to:
( | )
GD | MAX
TH | J
MAX | dv

dt
C
V | 0.007 T 25 R | ⎟
⎠

⎞ ⎜
⎝

⎛

⋅ − | ⋅ | − =

where RMAX=RLO+RGATE+RG,I.
Once the maximum pull down resistor value is given, the gate drive design can be executed. It should be taken into account that the driver’s pull down impedance is also temperature dependent. At elevated junction temperature the MOSFET based gate drive ICs exhibit higher output resistance than at 25°C where they are usually characterized.
Turn-off speed enhancement circuits can also be used to meet dv/dt immunity for the MOSFET since they can shunt out RGATE at turn-off and during the off state of the device. For instance, the simple pnp turn-off circuit of Figure 13 can boost the maximum dv/dt of the MOSFET. The equation modified by the effect of the beta of the pnp transistor yields the increased dv/dt rating of:
( )

GD

GATE LO
G,I
TH | J
C
β
R | R R
V | 0.007 T 25
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
⎛ | +
+
− | ⋅ | − =

In the dv/dt calculations a returning factor is the internal gate resistance of the MOSFET, which is not defined in any data sheet. As pointed out earlier, this resistance depends on the material properties used to distribute the gate signal, the cell density, and the cell design within the semiconductor.
SYNCHRONOUS RECTIFIER DRIVE The MOSFET synchronous rectifier is a special case of ground referenced switches. These devices are the same N-channel MOSFETs used in traditional applications, but applied in low voltage outputs of the power supplies instead of rectifier diodes. They usually work with a very limited drain-to-source voltage swing, therefore, their CDS and CGD capacitors exhibit relatively large capacitance values. Moreover, their application is unique because these devices are operated in the fourth quadrant of their V-I plane. The current is flowing from the source toward the drain terminal. That makes the gate drive signal kind of irrelevant. If the circumstances, other components around the synchronous switch require, current will flow in the device, either through the resistive channel or through the parasitic body diode of the MOSFET. The easiest model to examine the switching behavior of the MOSFET synchronous rectifier is a simplified buck power stage where the rectifier diode is replaced by the QSR transistor as shown in Figure

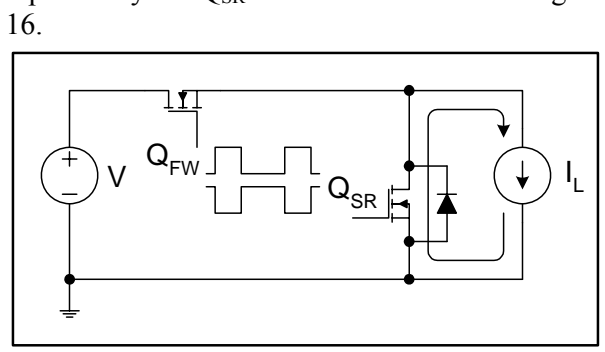
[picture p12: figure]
QFW; QSR

Figure 16. Simplified synchronous rectification model
The first thing to recognize in this circuit is that the operation of the synchronous rectifier MOSFET depends on the operation of another controlled switch in the circuit, namely the forward switch, QFW. The two gate drive waveforms are not independent and specific timing criteria must be met. Overlapping gate drive signals would be fatal because the two MOSFETs would short circuit the voltage source without any significant current limiting component in the loop. Ideally, the two switches would turn-on and off simultaneously to prevent the body diode of the QSR MOSFET to turn-on. Unfortunately, the window of opportunity to avoid body diode conduction is very narrow. Very accurate, adaptive timing and fast switching speeds are required, which are usually out of reach with traditional design techniques.

Consequently, in most cases a brief period – from 20ns to 80ns – of body diode conduction precedes the turn-on and follows the turn-off of the synchronous MOSFET switch.
Gate charge
During the body diode conduction period the full load current is established in the device and the drain-to-source voltage equals the body diode forward voltage drop. Under these conditions the required gate charge to turn the device on or off is different from the gate charge needed in traditional first quadrant operation. When the gate is turned-on, the drain-to-source voltage is practically zero and the CGD and CDS capacitors are discharged. Also, the Miller effect is not present, there is no feedback between the drain and gate terminals. Therefore, the required gate charge equals the charge needed to raise the voltage across the gate-to-source and gate-to-drain capacitors from 0V to the final VDRV level. For an accurate estimate, the low voltage average value of the CGD capacitor between 0V and VDRV has to be determined according to:

DRV

DS,SPEC
GD,SR | RSS.SPEC | 0.5 V

V
C | 2 C | ⋅ = ⋅ | ⋅

The following equation can then be used to estimate the total gate charge of the synchronous MOSFET rectifier:
( | ) QQ,SR | CGS | CGD,SR | VDRV = | + | ⋅

This value is appreciably lower than the total gate charge listed in the MOSFET data sheets. The same MOSFET with an identical driver circuit used for synchronous rectification can be turned on or off quicker than if it would be driven in its first quadrant operation. Unfortunately, this advantage can not be realized since the low RDS(on) devices, applicable for synchronous rectification, usually have pretty large input and output capacitances due to their large die size. Another important note from driver power dissipation point of view is that the total gate charge value from the data sheet should be considered. Although the gate charge delivered by the driver during turn-on is less than the typical number listed in the data sheet, that covers a portion of the total charge passing through the driver output impedance. Before turn-on, while the drain-to-source voltage changes across the device, the Miller charge provided by the power stage must flow through the driver of the synchronous MOSFET causing additional power dissipation. This phenomenon can be seen in Figure 17, which is part of the next discussion on dv/dt considerations.
The turn-off procedure of the synchronous MOSFET obeys the same rules as the turn-on
procedure, | therefore | all | the | previous
considerations with respect to gate charge are applicable.
dv/dt considerations
Figure 17 shows the most important circuit and current components during the turn-on and turn-off procedures of QSR. Actually, it is more accurate to say that the switching actions taking place in QFW forces QSR to turn-on or off independently of its own gate drive signal.

Figure 17. Synchronous switching model The turn-on of QSR starts with the turn-off of QFW. When the gate drive signal of QFW transitions from high to low, the switching node transitions from the input voltage level to GND. The current stays in the forward switch until the CRSS capacitor is discharged and the body diode of QSR is forward biased. At that instant the synchronous MOSFET takes over the current flow and QFW turns off completely. After a short delay dominated by the capabilities of the controller, the gate drive signal of QSR is applied and the MOSFET is turned on. At that time the current transfers from the body diode to the channel of the device.
At the end of the conduction period of QSR the MOSFET must be turned off. This procedure is initiated by removing the drive signal from the gate of the synchronous switch. This event itself will not cause the turn-off of the device. Instead, it will force the current to flow in the body diode instead of the channel. The operation of the circuit is indifferent to this change. Current starts to shift from QSR to QFW when the gate of the forward switch transitions from low to high. Once the full load current is taken over by QFW and the body diode is fully recovered, the switching node transitions from GND to the input voltage level. During this transition the CRSS capacitor of QSR is charged and the synchronous MOSFET is susceptible to dv/dt induced turn-on. Summarizing this unique operation of the synchronous MOSFET and its gate drive, the most important conclusion is to recognize that both turn-on and turn-off dv/dt of the synchronous MOSFET is forced on the device by the gate drive characteristics (i.e. the switching speed) of the forward switch. Therefore, the two gate drive circuits should be designed together to ensure that their respective speed and dv/dt limit matches under all operating conditions. This can be ensured by adhering to the steps of the following simple calculations:
( | )
( | )
TURN ON(FW) | MAX(SR)
LO(SR) | GATE(SR) | G,I(SR) | RSS(SR)

TH(SR)

MAX(SR)

HI(FW) | GATE(FW) | G,I(FW) | RSS(FW)
DRV | GS,PLATEAU(FW )

TURN ON(FW)

dt

dv
dt

dv

R | R | R | C

V
dt

dv

R | R | R | C
V | V
dt

dv

<

+ | + | ⋅ =
+ | + | ⋅

− =

−

−

Assuming the same devices for QSR and QFW, no external gate resistors, and that the internal gate resistance is negligible compared to the drivers output impedance, the ratio of the driver output impedances can be approximated by:

DRV GS,PLATEAU(FW ) TH(SR)

HI(FW)

LO(SR)

V V V
R

R
− ≤

A typical example with logic level MOSFETs driven by a 10V drive signal would yield a ratio of 0.417, which means that the pull down drive impedance of QSR must be less than 42% of the pull up drive impedance of QFW. When carrying out these calculations, remember that every parameter except VDRV is temperature dependent and their values might have to be adjusted to reflect the worst case operating conditions of the design.
HIGH SIDE NON-ISOLATED GATE DRIVES
High side non-isolated gate drive circuits can be classified by the device type they are driving or by the type of drive circuit involved. Accordingly, they are differentiated whether P-channel or N-channel devices are used or whether they implement direct drive, level shifted drive, or bootstrap technique. Which ever way, the design of high side drivers need more attention and the following checklist might be useful to cover all aspects of the design:
- Efficiency
- Bias / power requirements
- Speed limitations
- Maximum duty-cycle limit
- dv/dt implications
- Start-up conditions
- Transient operation
- Bypass capacitor size
- Layout, grounding considerations

High side drivers for P-channel devices
In this group of circuits the source terminal of the P-channel MOSFET switch is connected to the positive input rail. The driver applies a negative amplitude turn-on signal to the gate with respect to the source of the device. This means that the output of the PWM controller has to be inverted and referenced to the positive input rail. Because the input voltage can be considered as a DC voltage source, high side P-channel drivers do not have to swing between large potential differences on the switching frequency basis, but they must work over the entire input voltage range. Moreover, the driver is referenced to an AC ground potential due to the low AC impedance of the input voltage source.
P-channel direct drive
The easiest case of P-channel high side drivers is direct drive, which can be implemented if the maximum input voltage is less then the gate-to-source breakdown voltage of the device. A typical application area is 12V input DC/DC converters using a P-channel MOSFET, similar to the schematic in Figure 18. Note the inverted PWM output signal is readily available in some

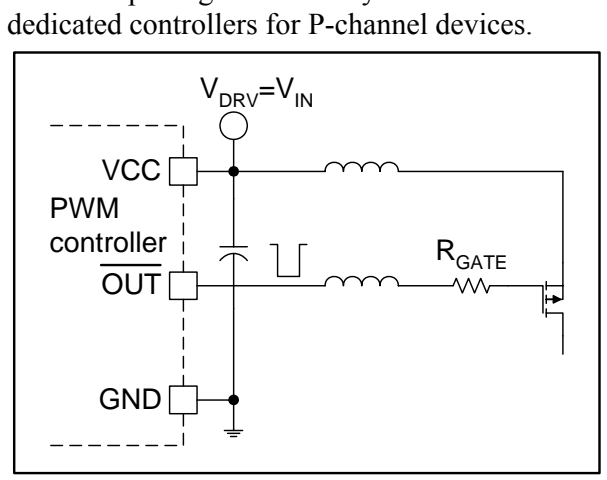
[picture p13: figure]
dedicated controllers for P-channel devices.; RGATE; VCC; OUT; GND; VDRV=VIN; PWM controller

Figure 18. Direct drive for P-channel MOSFET The operation of the circuit is similar to the ground referenced direct driver for N-channel devices. The significant difference is the path of the gate drive current, which never flows in the ground connections. Instead, the high charge and discharge currents of the gate are conducted by the positive rail interconnection. Consequently, to minimize the loop inductance in the gate drive, wide traces or a plane is desirable for the positive input.
P-channel level shifted drive
For input voltages exceeding the gate-to-source voltage limit of the MOSFET, level shifted gate drive circuits are necessary. The simplest level shift technique is using an open collector driver as shown in Figure 19. Unfortunately, open collector level shifters are not suitable for driving MOSFETs directly in a high speed application.

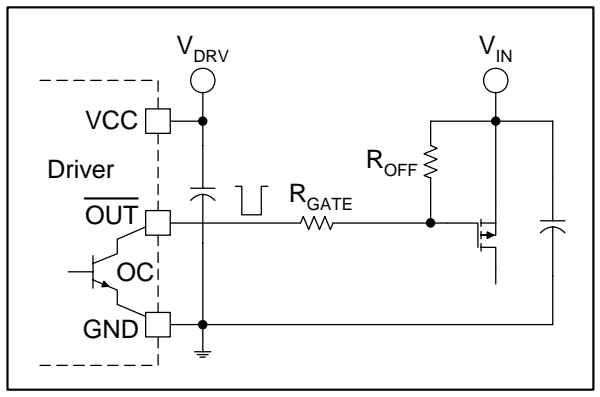
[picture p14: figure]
VCC; OUT; GND; VDRV; Driver; VIN; RGATE; ROFF

Figure 19. Open collector drive for PMOS device Problems are numerous with this implementation starting with the limited input voltage range due to the voltage rating of the open collector transistor. But the most inhibiting obstacle is the high drive impedance. Both resistors, ROFF and RGATE must be a high value resistor to limit the continuous current in the driver during the conduction period of the switch. Furthermore, the gate drive amplitude depends on the resistor divider ratio and the input voltage level. Switching speed and dv/dt immunity are severely limited which excludes this circuit from switching applications. Nevertheless, this very simple level shift interface can be used for driving switches in inrush current limiters or similar applications where speed is not an important consideration.
Figure 20 shows a level shifted gate drive circuit which is suitable for high speed applications and works seamlessly with regular PWM controllers. The open collector level shift principle can be easily recognized at the input of a bipolar totem-pole driver stage. The level shifter serves two purposes in this implementation; it inverts the PWM output and references the PWM signal to the input rail.
The turn-on speed is fast, defined by RGATE and R2. During the on-time of the switch a small DC current flows in the level shifter keeping the driver biased in the right state. Both the gate drive power and the level shift current are provided by the positive input of the power stage which is usually well bypassed.

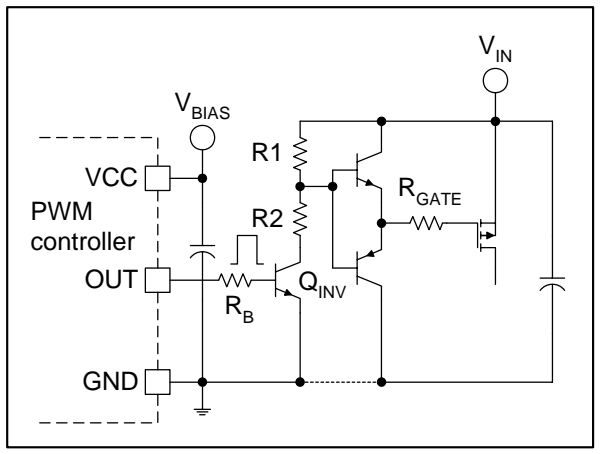
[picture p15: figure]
VCC; OUT; GND; VBIAS; PWM controller; VIN; RGATE; QINV RB

Figure 20. Level shifted P-channel MOSFET driver
The power consumption of the driver has a frequency dependent portion based on the gate charge of the main switch and a duty-cycle and input voltage dependent portion due to the current flowing in the level shifter.

R1 R2

V D P | Q V | f | IN | MAX
DRIVE | G | DRV | DRV
+
⋅ = | ⋅ | ⋅ | +

One of the drawbacks of this circuit is that VDRV is still a function of the input voltage due to the R1, R2 divider. In most cases protection circuits might be needed to prevent excessive voltage across the gate-to-source terminals. Another potential difficulty is the saturation of the npn level shift transistor, which can extend the turn-off time otherwise defined by R1 and RGATE. Fortunately both of these shortcomings can be addressed by moving R2 between the emitter of QINV and GND. The resulting circuit provides constant gate drive amplitude and fast, symmetrical switching speed during turn-on and turn-off. The dv/dt immunity of the driver scheme is primarily set by the R1 resistor. A lower value resistor will improve the immunity against dv/dt induced turn-on but also increases the power losses of the level shifter. Also, notice that this solution has a built in self-biasing mechanism during power up. While the PWM controller is still inactive, QINV is off and the gate of the main MOSFET is held below its threshold by R1 and the upper npn transistor of the totem-pole driver. Pay specific attention to rapid input voltage transients though as they could cause dv/dt induced turn-on during the off state of the P-channel MOSFET transistor.
In general, the DC level shift drivers have relatively low efficiency and are power dissipation limited above a certain input voltage level. The fundamental trade-off is to balance the switching speed and the power consumption of the level shifter to meet all requirements under the entire input voltage range.
High side direct drivers for N-channel devices The majority of power supply applications utilize N-channel MOSFETs as the main power switch because of their lower price, higher speed and lower on-resistance. Using N-channel devices as a high side switch necessitates a gate drive circuit which is referenced to the source of the MOSFET. The driver must tolerate the violent voltage swings occurring during the switching transitions and drive the gate of the MOSFET above the positive supply rail of the power supply. In most cases, the gate drive voltage must be above the highest DC potential available in the circuit. All these difficulties make the high side driver design a challenging task.
High side direct drive for N-channel MOSFET In the easiest high side applications the MOSFET can be driven directly by the PWM controller or by a ground referenced driver. Two conditions must be met for this application:
IN | DRV | GS,Miller
DRV | GS,MAX
V | V | V
V | V
< | −

<

A typical application schematic is illustrated in Figure 21 with an optional pnp turn-off circuit.

Figure 21. Direct drive of N-channel MOSFET

Looking at the basic operation of the circuit – neglect the pnp turn-off transistor for now – there are two major differences with this configuration compared to the ground referenced drive scheme. Since the drain is connected to the positive DC input rail, the switching action takes place at the source terminal of the device. It is still the same clamped inductive switching with identical turn-on and turn-off intervals. But from gate drive design point of view this is a completely different circuit. Notice that the gate drive current can not return to ground at the source terminal. Instead it must go through the load, connected to the source of the device. In discontinuous inductor current mode the gate charge current must go through the output inductor and the load. In continuous inductor current mode, however, the loop can be closed through the conducting pn junction of the rectifier diode. At turn-off, the gate discharge current comes through the rectifier diode connected between ground and the source of the MOSFET. In all operating modes, both the charge and discharge currents of the CGD capacitor flow through the high frequency bypass capacitor of the power stage.
The net result of all these differences is the increased parasitic source inductance due to more components and larger loop area involved in the gate drive circuitry. As presented earlier, the source inductance has a negative feedback effect on the gate drive and slows down the switching actions in the circuit.
The other significant difference in high side direct drive is the behavior of the source – the switching node of the circuit. Paying close attention to the source waveform of the MOSFET during turn-off, a large negative voltage can be observed. Figure 22 illustrates this rather complex switching action.
As the turn-off is initiated by pulling the gate terminal toward ground, the input capacitances of the MOSFET are quickly discharged to the Miller plateau voltage. The device is still fully on, the entire load current is flowing through the drain to the source and the voltage drop is small. Next, in the Miller region, the MOSFET works as a source follower.

The source falls together with the gate, and while the voltage across the drain-to-source increases, the gate-to-source voltage remains constant at the VGS,Miller level. The dv/dt is limited by the gate drive impedance and the CGD capacitor of the device. Once the source falls 0.7V or so below ground, the rectifier diode is supposed to clamp

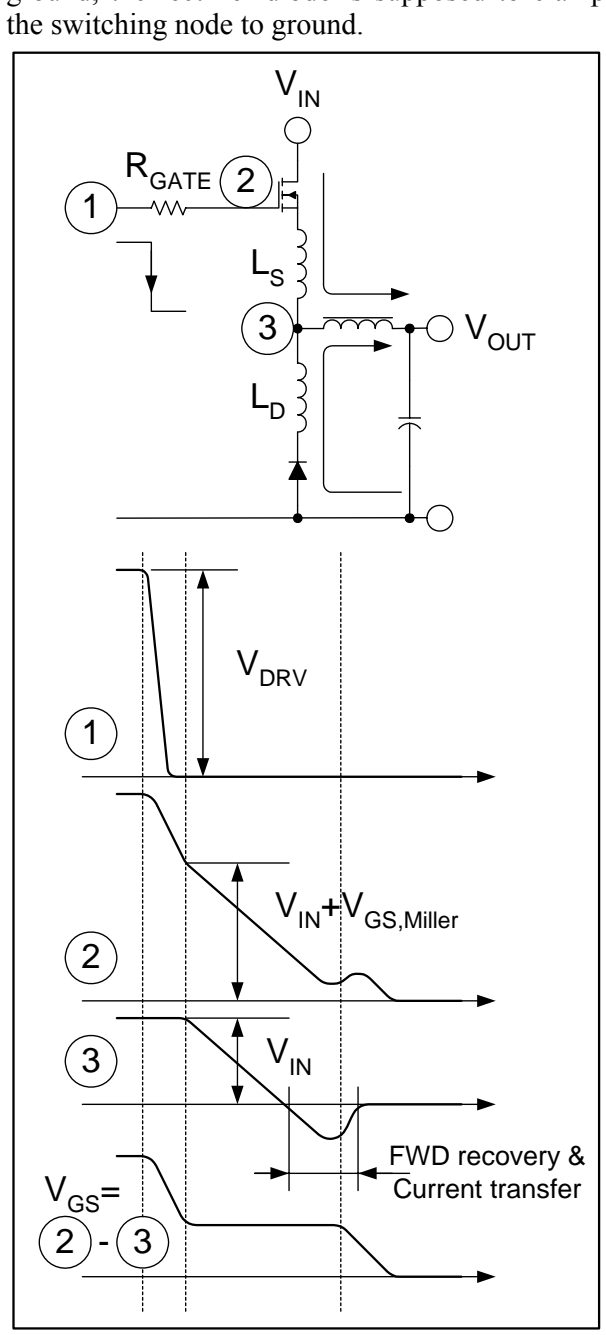
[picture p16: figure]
the switching node to ground.; VIN; RGATE; VOUT; VGS=; VDRV; VIN+VGS,Miller; FWD recovery & Current transfer

Figure 22. Turn-off of high side N-channel MOSFET

Actually, the source can fall way below ground for a short period of time until the rectifier diode gets through its forward recovery process and the current overcomes the effect of the parasitic inductances. After the load current is completely transferred from the MOSFET to the diode, the switching node can return to its final voltage, a diode drop below ground.
This negative excursion of the source voltage represents a significant problem for the gate drive circuit. Slow diodes, high parasitic inductance values can cause excessive negative voltage at the source of the MOSFET, and can pull the output pin of the driver below ground. To protect the driver, a low forward voltage drop Schottky diode might be connected between the output pin and ground as indicated in Figure 21. Another aspect to consider is when the gate terminal reaches 0V, the gate discharge current would become zero. Further negative pull on the gate terminal and the MOSFET starts turning back on. Ultimately the system finds a very delicate equilibrium where the gate discharge current and the voltage drop across the parasitic inductances result the same di/dt in the device current.
Even the optional turn-off speed-up circuit shown in Figure 21 can not help during the negative voltage spike of the switching junction. The pnp transistor will turn-off when the gate falls to a VBE above ground and the MOSFET is left on its own during the negative voltage transient. Also, pay attention to the reduced noise tolerance during the off state of the main switch. The source is several hundred millivolts below ground and the gate is held at approximately 0.7V above ground. This positive voltage across the gate with respect to the source is dangerously close to the threshold voltage especially for logic level devices and at elevated temperatures. Bootstrap gate drive technique
Where input voltage levels prohibit the use of direct gate drive circuits for high side N-channel MOSFETs, the principle of bootstrap gate drive technique can be considered. This method utilizes a gate drive and accompanying bias circuit, both referenced to the source of the main MOSFET transistor. Both the driver and the bias circuit swing between the two input voltage rails together with the source of the device. However, the driver and its floating bias can be implemented by low voltage circuit elements since the input voltage is never applied across their components. The driver and the ground referenced control signal are linked by a level shift circuit which must tolerate the high voltage difference and considerable capacitive switching currents between the floating high side and ground referenced low side circuits.
Discrete high performance floating driver
A typical implementation representing the bootstrap principle is displayed in Figure 23. The ground referenced PWM controller or MOSFET driver is represented by its local bypass capacitor and the output pin. The basic building blocks of the bootstrap gate drive circuit can be easily recognized. The level-shift circuit is comprised of the bootstrap diode QBST, R1, R2 and the level shift transistor, QLS. The bootstrap capacitor, CBST, a totem-pole bipolar driver and the usual gate resistor are the floating, source referenced part of the bootstrap solution.
This particular implementation can be used very effectively in 12V to approximately 24V systems with simple low cost PWM controllers which have no floating driver on board. It is beneficial that the IC voltage rating does not limit the input voltage level. Furthermore, the level shift circuit is a source switched small NMOS transistor which does not draw any current during the on time of the main MOSFET from the bootstrap capacitor. It is an important feature to maintain high efficiency in the level shifter, and to extend the maximum on-time of the main switch. The operation can be summarized as follows: when the PWM output goes high to turn on the main MOSFET, the level shift transistor turns off. R1 supports the base current to the upper npn transistor in the totem-pole driver and the main MOSFET turns on. The gate charge is taken from the bootstrap capacitor, CBST. As the switch turns on, its source swings to the positive input rail. The bootstrap diode and transistor block the input voltage and power to the driver is provided from the bootstrap capacitor. At turn-off, the PWM output goes low turning on the level shift transistor.

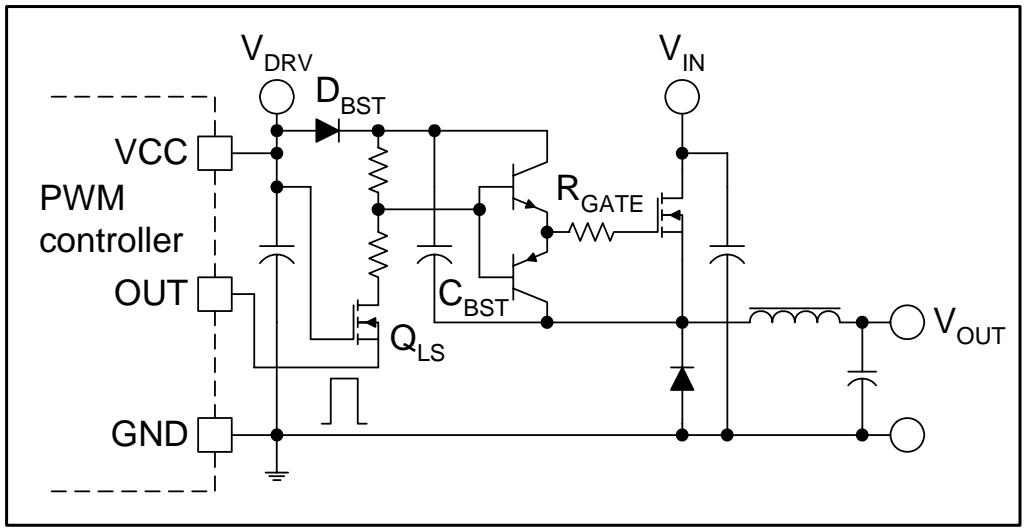
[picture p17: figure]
VCC; OUT; GND; VDRV; PWM controller; VIN; RGATE; VOUT; DBST; CBST; QLS

Figure 23. Integrated bootstrap driver Current starts to flow in R1 and R2 towards ground and the lower pnp transistor of the totem-pole driver turns on. As the gate of the main MOSFET discharges, the drain-to-source voltage increases and the source transitions to ground, allowing the rectifier to turn-on. During the off time of the main switch, the bootstrap capacitor is recharged to the VDRV level through the bootstrap diode. This current is supplied by the CDRV bypass capacitor of the ground referenced circuitry and it goes through DBST, CBST, and the conducting rectifier component. This is the basic operating principle of the bootstrap technique. Integrated bootstrap drivers
In medium input voltage applications, mainly 24V or 48V telecom systems, most of the bootstrap components can be integrated into the PWM controller as illustrated in Figure 24.

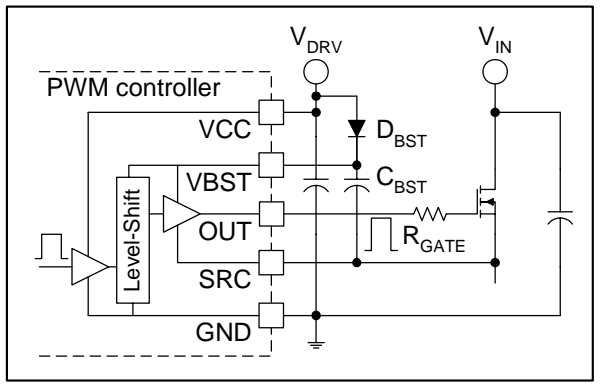
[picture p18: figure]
VCC; OUT; GND; PWM controller; VIN; RGATE; VDRV; SRC; VBST; Level-Shift; DBST; CBST

Figure 24. Integrated bootstrap driver

For even higher voltages, dedicated driver ICs are available to ease the design of bootstrap gate drive with up to 600V rating. These high voltage ICs are differentiated by their unique level shift design. In order to maintain high efficiency and manageable power dissipation, the level shifters should not draw any current during the on-time of the main switch. Even a modest 1mA current in the level shift transistors might result in close to 0.5W worst case power dissipation in the driver IC.
A widely used technique for these applications is called pulsed latch level translators and they are

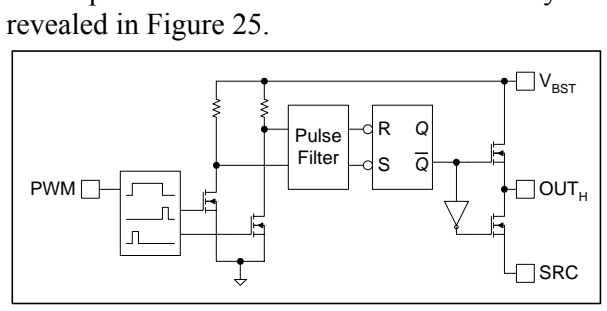
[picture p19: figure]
revealed in Figure 25.; VBST; OUTH; SRC; Pulse Filter; PWM

Figure 25. Typical level shifter in high voltage driver IC
As indicated in the drawing, the PWM input signal is translated to ON/OFF commands. The short pulses generated at the rising and falling edges drive the level shift transistor pair which interfaces with the high side circuitry. Accordingly, the floating portion of the driver is modified as well, the level shifted command signals have to be differentiated from noise and must be latched for proper action. This operation results in lower power dissipation because of the short duration of the current in the level shifter but lowers noise immunity since the command signal is not present at the input of the driver continuously. The typical pulse width in a 600V rated pulsed latch level translator is around 120 nanoseconds. This time interval adds to natural delays in the driver and shows up as turn-on and turn-off delays in the operation and is indicated in the data sheet of the drivers. Due to the longer than optimum delays, the operating frequency range of the high voltage gate driver ICs is limited below a couple of hundreds of kHz.
Some lower voltage high side driver ICs (up to 100V) use continuous current DC level shift circuits to eliminate the delay of the pulse discriminator, therefore they support higher operating frequency.
Bootstrap switching action
Bootstrap gate drive circuits are used with high side N-channel MOSFET transistors as shown in Figure 26. The switching transitions of the high side switch were explored previously with respect to the high side N-channel direct drive scheme and are equally applicable with bootstrap

The biggest difficulty with this circuit is the negative voltage present at the source of the device during turn-off. As shown previously, the amplitude of the negative voltage is proportional to the parasitic inductance connecting the source of the main MOSFET to ground (including the parasitic inductance associated with the rectifier) and the turn-off speed (di/dt) of the device as determined primarily by the gate drive resistor, RGATE and input capacitor, CISS. This negative voltage can be serious trouble for the driver’s output stage since it directly affects the source pin – often called SRC or VS pin – of the driver or PWM IC and might pull some of the internal circuitry significantly below ground.
The other problem caused by the negative voltage transient is the possibility to develop an over voltage across the bootstrap capacitor. Capacitor CBST will be peak charged by DBST from CDRV. Since CDRV is referenced to ground, the maximum voltage which can build on the bootstrap capacitor is the sum of VDRV and the amplitude of the negative voltage at the source terminal. A small resistor in series with the bootstrap diode can mitigate the problem. Unfortunately, the series resistor does not provide a foolproof solution against an over voltage and it

also slows down the recharge process of the

Figure 26. High voltage driver IC for bootstrap gate drive

A circuit to deliver very effective protection for the SRC pin is given in Figure 27. It involves relocating the gate resistor from the gate to the source lead between the driver and the main MOSFET and adding a small, low forward voltage drop Schottky diode from ground to the

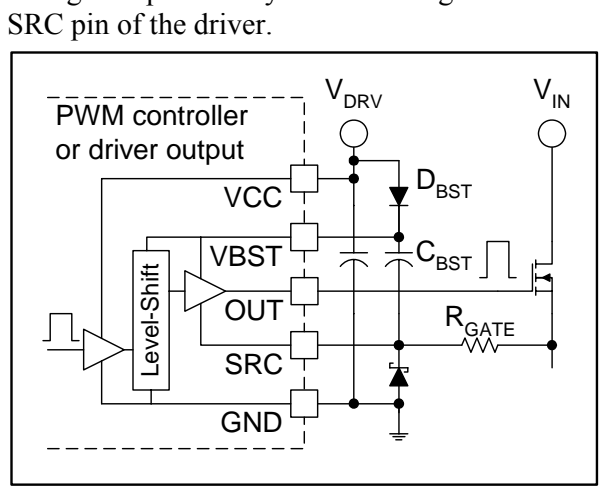
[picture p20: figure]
SRC pin of the driver.; VCC; OUT; GND; PWM controller or driver output; VIN; RGATE; VDRV; SRC; VBST; Level-Shift; CBST; DBST

Figure 27. Protecting the SRC pin
In this circuit, RGATE has a double purpose; it sets the turn-on and turn-off speed in the MOSFET and also provides current limiting for the Schottky diode during the negative voltage transient of the source terminal of the main switch. Now, the switching node can swing several volts below ground without disturbing the operation of the driver. In addition, the bootstrap capacitor is protected against over voltage by the

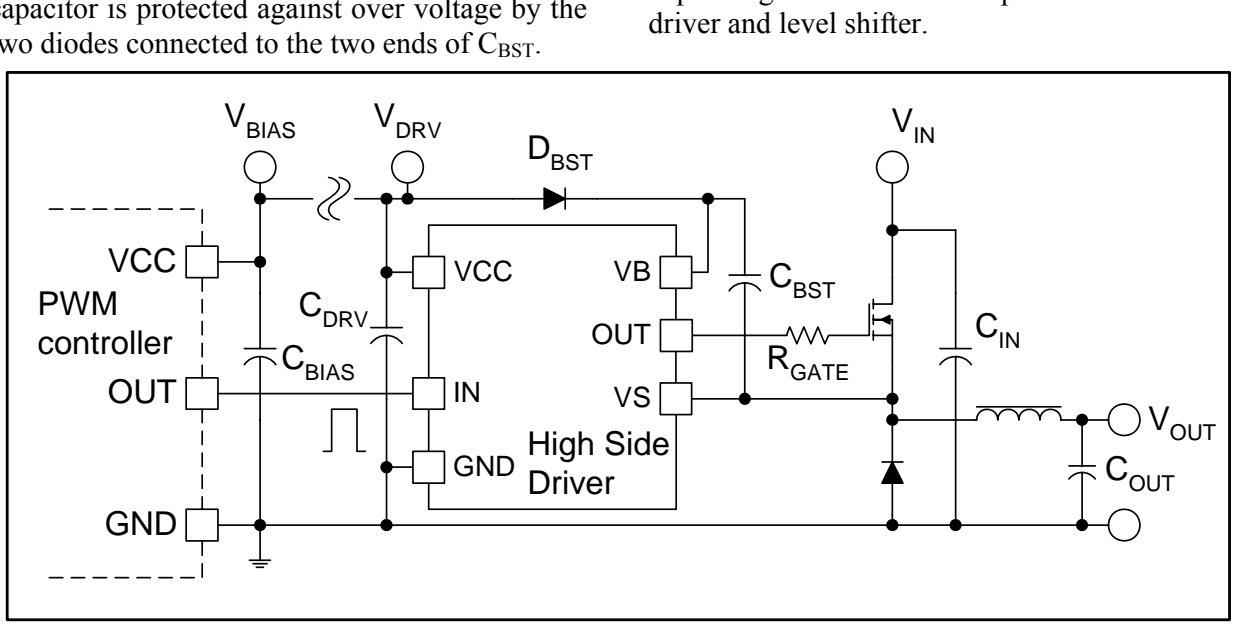
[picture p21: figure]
driver and level shifter.; VIN; RGATE; High Side Driver; VCC; OUT; GND; VBIAS; PWM controller; VOUT; CBST CDRV; CBIAS; DBST; VDRV; CIN; COUT

two diodes connected to the two ends of CBST.

The only potential hazard presented by this circuit is that the charge current of the bootstrap capacitor must go through RGATE. The time constant of CBST and RGATE slows the recharge process which might be a limiting factor as the PWM duty ratio approaches unity.
Bootstrap biasing, transient issues and start-up Figure 28 shows a typical application diagram of the bootstrap gate drive technique. There are four important bypass capacitors marked on the schematic.
The bootstrap capacitor, CBST is the most important component from the design point of view, since it has to filter the high peak current charging the gate of the main MOSFET while providing bias for the source referenced floating circuitry. In every switching cycle during normal operation, the bootstrap capacitor provides the total gate charge (QG) to turn-on the MOSFET, the reverse recovery charge (QRR) and leakage current of the bootstrap diode (ILK,D), the quiescent current of the level shifter (IQ,LS) and the gate driver (IQ,DRV), and the leakage current between the gate-source terminals (IGS), including the current drawn by a potential gate-to-source pull down resistor. Some of these currents flow only during the on-time of the main switch and some of them might be zero depending on the actual implementation of the

Figure 28. Bootstrap bypassing example

Assuming steady state operation, the following general equation can be used to calculate the bootstrap capacitor value to achieve the targeted ripple voltage, ΔVBST:

BST

DRV

MAX
G | RR | BST
BST | ΔV

f

D Q | Q | I

C

+ | + | ⋅
=

where

BST | LK,D | Q,LS | Q,DRV | GS I | = I | + I | + I | + I
To finalize the bootstrap capacitor value, two extreme operating conditions must be checked as well. During load transients it might be necessary to keep the main switch on or off for several switching cycles. In order to ensure uninterrupted operation under these circumstances, the CBST capacitor must store enough energy to hold the floating bias voltage above the under voltage lockout threshold of the high side driver IC for an extended period of time.
Going from light load to heavy load, certain controllers can keep the main switch on continuously until the output inductor current reaches the load current value. The maximum on time (tON,MAX) is usually defined by the value and the voltage differential across the output inductor. For these cases, a minimum bootstrap capacitor value can be established as:
BST | UVLO
G | RR | BST | ON,MAX
BST,MIN | V | V
Q | Q | I | t
C | −
+ | + | ⋅ =

where VBST is the initial value of the bootstrap bias voltage across CBST and VUVLO is the under voltage lockout threshold of the driver. With a discrete floating driver implementation, VUVLO could be substituted by the minimum safe gate drive voltage.
Any load transient in the other direction will require pulse skipping when the MOSFET stays off for several switching cycles. When the output inductor current reaches zero, the source of the main switch will settle at the output voltage level. The bootstrap capacitor must supply all the usual discharge current components and store enough energy to be able to turn-on the switch at the end of the idle period. Similar to the previous transient mode, a minimum capacitor value can be calculated as:
( | )
BST | UVLO
G | LK,D | Q,LS | Q,DRV | OFF,MAX
BST,MIN | V | V
Q | I | I | I | t
C | −
+ | + | + | ⋅ =

In certain applications, like in battery chargers, the output voltage might be present before input power is applied to the converter. In these cases, the source of the main MOSFET and the negative node of CBST are sitting at the output voltage and the bootstrap diode might be reverse biased at start-up. Delivering the initial charge to the bootstrap capacitor might not be possible depending on the potential difference between the bias and output voltage levels. Assuming there is enough voltage differential between the input and output voltages, a simple circuit comprised of RSTART resistor, DSTART diode, and DZ zener diode can solve the start-up problem as shown in Figure 29.

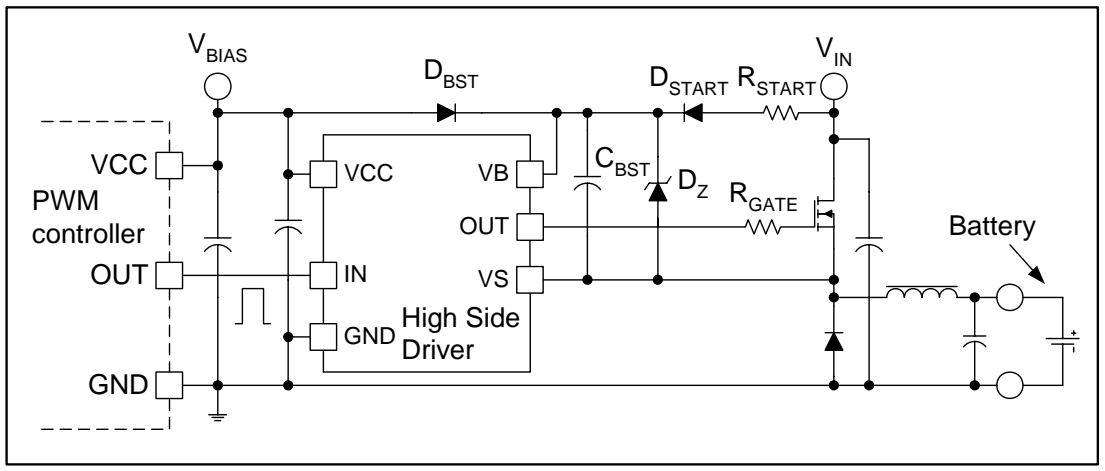
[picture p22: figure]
VCC; OUT; GND; VBIAS; PWM controller; VIN; RGATE; Battery; RSTART; High Side Driver; DSTART; CBST; DBST

Figure 29. Bootstrap start-up circuit

In this start-up circuit, DSTART serves as a second bootstrap diode used for charging the bootstrap capacitor at power up. CBST will be charged to the zener voltage of DZ which is supposed to be higher than the driver’s bias voltage during normal operation. The charge current of the bootstrap capacitor and the zener current are limited by the start-up resistor. For best efficiency the value of RSTART should be selected to limit the current to a low value since the second bootstrap path through the start-up diode is permanently in the circuit.
Grounding considerations
There are three important grounding issues which have to be addressed with respect to the optimum layout design of the bootstrap gate drivers with high side N-channel MOSFETs. Figure 28 can be used to identify the most critical high current loops in a typical application.
The first focus is to confine the high peak currents of the gate in a minimal physical area. Considering the path the gate current must pass through, it might be a challenging task. At turn-on, the path involves the bootstrap capacitor, the turn-on transistor of the driver, the gate resistor, the gate terminal, and finally, the loop is closed at the source of the main MOSFET where CBST is referenced. The turn-off procedure is more complicated as the gate current has two separate components. The discharge current of the CGS capacitor is well localized, it flows through the gate resistor, the turn-off transistor of the driver and from the source to the gate of the power MOSFET. On the other hand, the CGD capacitor’s current must go through RGATE, the turn-off transistor of the driver, the output filter, and finally the input capacitor of the power stage (CIN). All three loops carrying the gate drive currents have to be minimized on the printed circuit board.
The second high current path includes the bootstrap capacitor, the bootstrap diode, the local ground referenced bypass capacitor of the driver, and the rectifier diode or transistor of the power stage. CBST is recharged on the cycle-by-cycle basis through the bootstrap diode from the ground referenced driver capacitor, CDRV, connected from the anode of DBST to ground. The recharge happens in a short time interval and involves high peak current. Therefore, the high side driver must be bypassed locally on its input side as well. According to the rule-of-thumb, CDRV should be an order of magnitude larger than CBST. Minimizing this loop area on the printed circuit board is equally important to ensure reliable operation.
The third issue with the circuit is to contain the parasitic capacitive currents flowing between power ground and the floating circuitry in a low impedance loop. The goal is to steer these currents away from the ground of the sensitive analog control parts. Figure 30 reveals the parasitic capacitive current paths in two representative applications with high side driver

Figure 30. Capacitive currents in high side applications
Single high side driver ICs usually have only one GND connection. Since the capacitive currents must return to the ground potential of the power stage, the low side portion of the IC should be
referenced | to | power | ground. | This | is
counterintuitive, since the control signal of the driver is referenced to signal ground. Nevertheless, eliminating the high capacitive current component between analog and power ground will also ensure that the potential difference between the two grounds are minimized.
The situation is greatly improved with general purpose half bridge driver ICs which contain one low side and one high side driver in the same package. These circuits have two ground connections usually labeled as GND and COM, providing more flexibility in layout. To return the capacitive currents to power ground in the shortest possible route, the COM pin is connected to power ground. The GND pin can be utilized to provide connection to the signal ground of the controller to achieve maximum noise immunity. For completeness, the bypass capacitor of the PWM controller should be mentioned as well, which is placed near to the VCC and GND pins of the IC. Referring to Figure 28 again, CBIAS is a relatively small capacitor with respect to CBST and CDRV since it provides only high frequency bypassing and it is not involved in the gate drive process.
AC COUPLED GATE DRIVE
CIRCUITS
AC coupling in the gate drive path provides a simple level shift for the gate drive signal. The primary purpose of AC coupling is to modify the turn-on and turn-off gate voltages of the main MOSFET as opposed to high side gate drives where the key interest is to bridge large potential differences. In a ground referenced example like the one in Figure 31, the gate is driven between -VCL and VDRV-VCL levels instead of the original output voltage levels of the driver, 0V and VDRV. The voltage, VCL is determined by the diode clamp network and it is developed across the coupling capacitor. The benefit of this technique is a simple way to provide negative bias for the gate at turn-off and during the off state of the switch to improve the turn-off speed and the dv/dt immunity of the MOSFET. The trade-off is slightly reduced turn-on speed and potentially higher RDS(on) resistance because of the lower positive drive voltage.
The fundamental components of AC coupling are the coupling capacitor CC and the gate-to-source load resistor RGS.

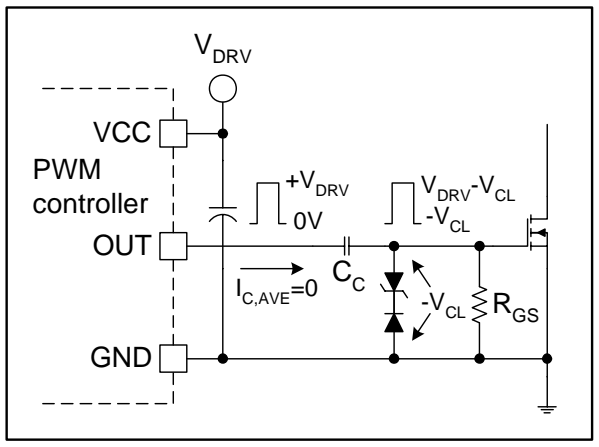
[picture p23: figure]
RGS; VCC; OUT; GND; VDRV; PWM controller; +VDRV; VDRV-VCL; -VCL; C,AVE=0

Figure 31. Capacitively coupled MOSFET gate drive
The resistor plays a crucial role during power up, pulling the gate low. This is the only mechanism keeping the MOSFET off at start up due to the blocking effect of the coupling capacitor between the output of the driver and the gate of the device. In addition, RGS provides a path for a current across the coupling capacitor. Without this current component the voltage would not be allowed to build across CC. Theoretically, in every switching cycle the same amount of total gate charge would be delivered then removed through the capacitor and the net charge passing through CC would be zero.
The same concept can be applied for steady state operation to determine the DC voltage across the coupling capacitor with RGS in the circuit. Assuming no clamp circuitry, a constant VC voltage across the capacitor, and a constant duty cycle D, the current of RGS can be represented as an additional charge component passing through CC. Accordingly, the total charge delivered through the coupling capacitor during turn-on and consecutive on-time of the MOSFET is:
GS | DRV
DRV | C
C,ON | G | f

D
R
V | V Q | Q | ⋅ − = | +

Following the same considerations for the turn-off and successive off-time of the switch, the total charge can be calculated as:

GS DRV

C
C,OFF | G | f

1 D
R
V Q | Q | − = | + | ⋅

For steady state operation, the two charges must be equal.

Solving the equations for VC determines the voltage across the coupling capacitor:

VC = VDRV ⋅D
This well know relationship highlights the duty ratio dependency of the coupling capacitor voltage. As duty cycle varies, VC is changing and the turn-on and turn-off voltages of the MOSFET adjust accordingly. As Figure 32 exemplifies, at low duty cycles the negative bias during turn-off is reduced, while at large duty ratios the turn-on voltage becomes insufficient. Normalized Steady State DC Voltage ⁽VC/VDRV⁾ Across CC

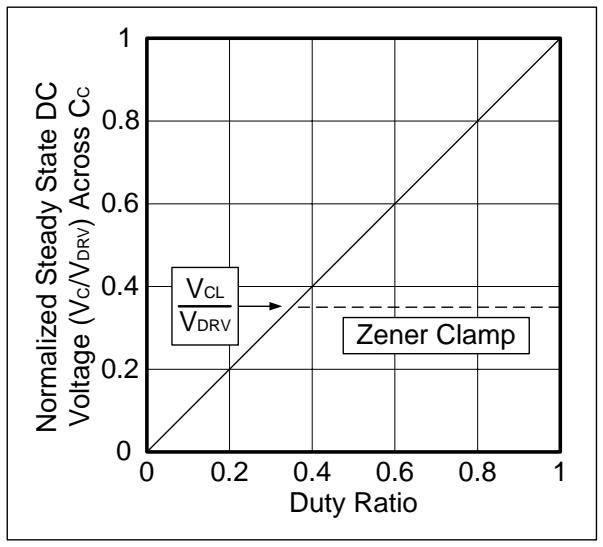
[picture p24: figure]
Duty Ratio; Zener Clamp; VCL; VDRV

Figure 32. Normalized coupling capacitor voltage as a function of duty ratio
The inadequate turn-on voltage at large duty ratios can be resolved by using a clamp circuit connected in parallel to RGS as shown in Figure
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

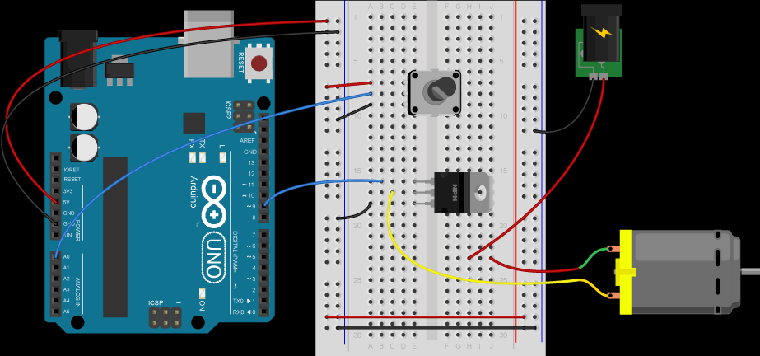
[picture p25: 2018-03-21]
Wiring_Diagram.png

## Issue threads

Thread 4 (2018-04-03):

Solder together the first prototype board

robinschiro, 2018-04-03:
- [x] De-solder the "white" LED, try to find actual white one.
- [x] Solder in all cables that are underneath the board
    - [x] Verify connectivity
- [x] Solder in all cables on top layer
    - [x] Initial set of wires
    - [x] Need to solder new ground wires + pot 5V line
    - [x] Verify connectivity
- [x] Solder in resistors
    - [x] LED resistors
    - [x] Base resistors
    - [x] Will need to find 2 additional 100 OHM resistors in lab
- [x] Solder in transistors
    - [x] Solder first 5
    - [x] Solder last one
- [x] Solder in potentiometer
- [x] Create solder bridges (excluding fuel injector cable connection points)
   - [x] Create most solder bridges
   - [x] Finish last few ground solder bridges for transistors
- [ ] Solder bridge VIN hole to pin
- [ ] Solder splice fuel injector cables to proper lower-gauge cables found in Garage
    - If Garage does not have proper cabling, then use the cables I already have
- [ ] Solder those cables into the board
   - [x] Solder first cable

robinschiro, 2018-04-03:
First day of soldering:
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

robinschiro, 2018-04-08:
Third day:
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

robinschiro, 2018-05-05:
Last day. All cables soldering onto the board!
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

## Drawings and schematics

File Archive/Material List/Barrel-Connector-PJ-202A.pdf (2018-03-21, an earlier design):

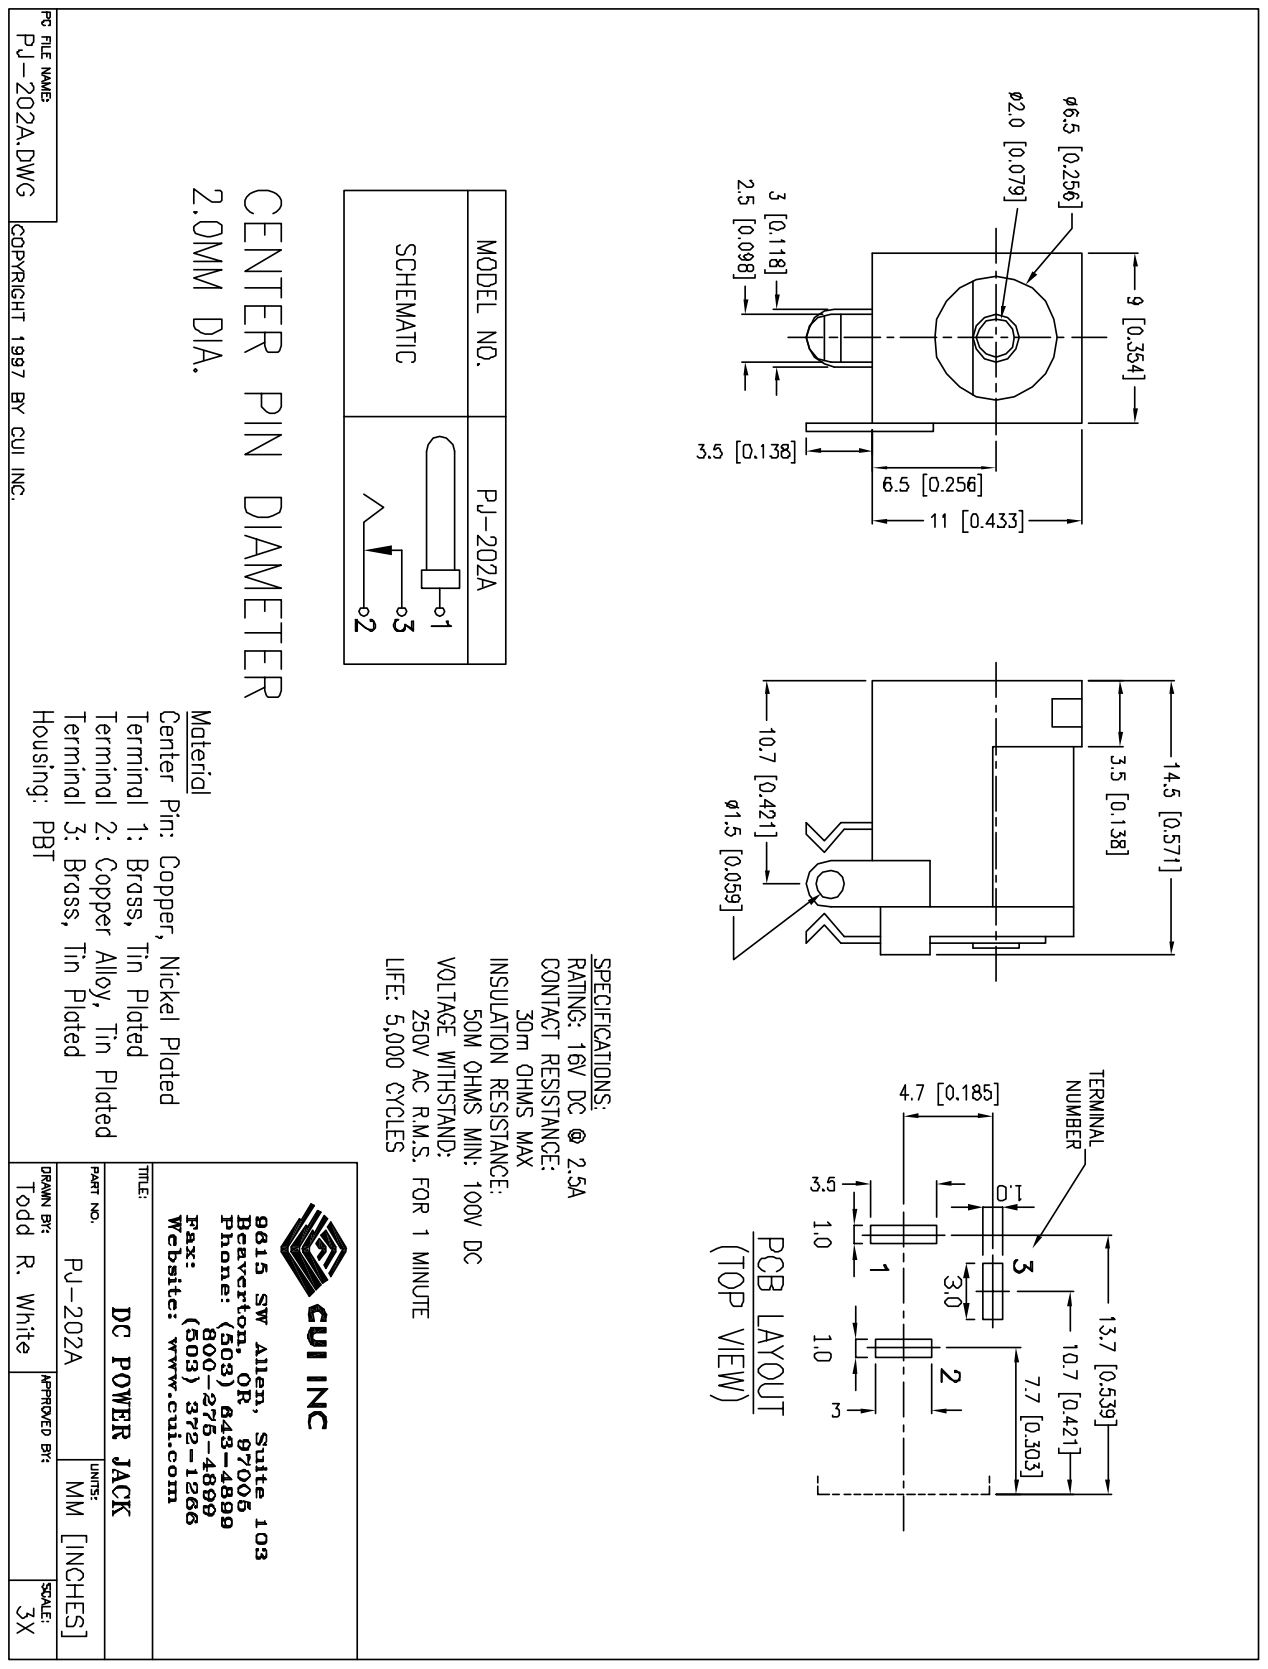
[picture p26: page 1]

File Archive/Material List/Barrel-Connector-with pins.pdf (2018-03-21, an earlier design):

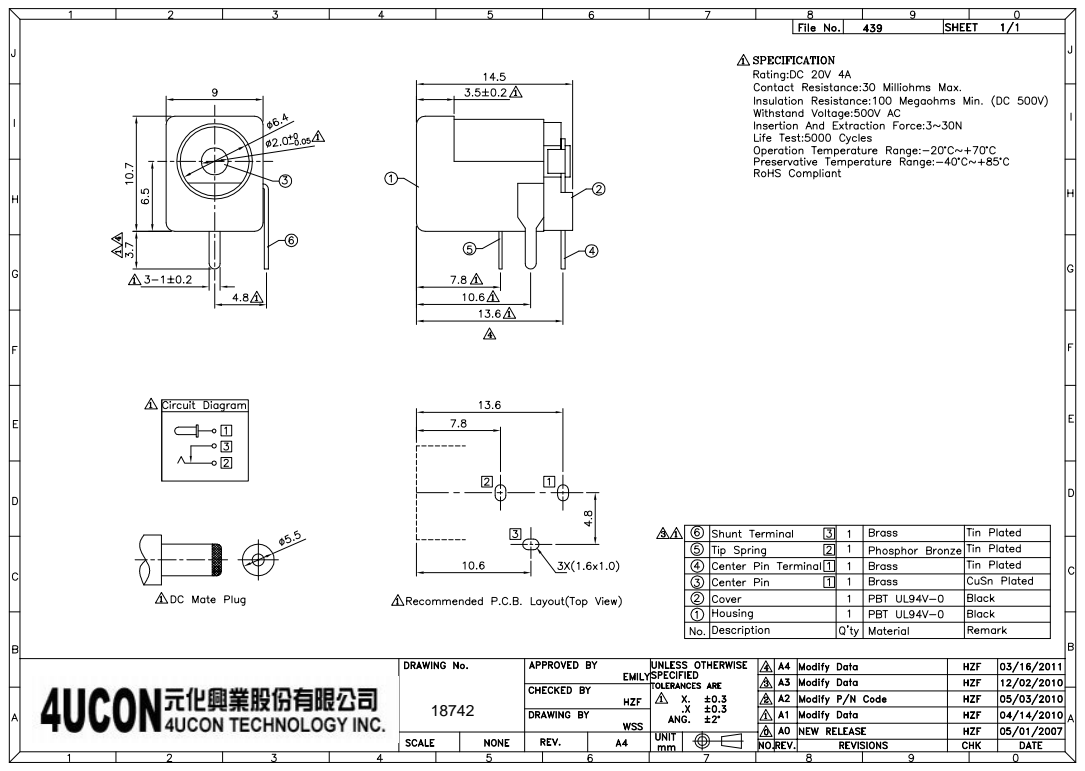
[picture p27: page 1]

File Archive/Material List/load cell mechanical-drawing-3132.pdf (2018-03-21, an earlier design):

# Mechanical Drawing 3132 - Micro Load Cell (0-780g) - CZL616C

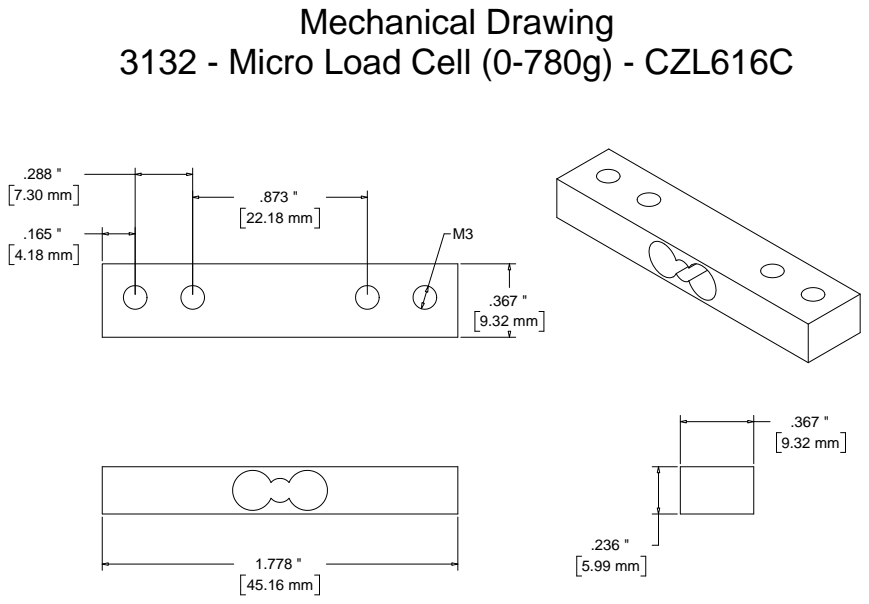
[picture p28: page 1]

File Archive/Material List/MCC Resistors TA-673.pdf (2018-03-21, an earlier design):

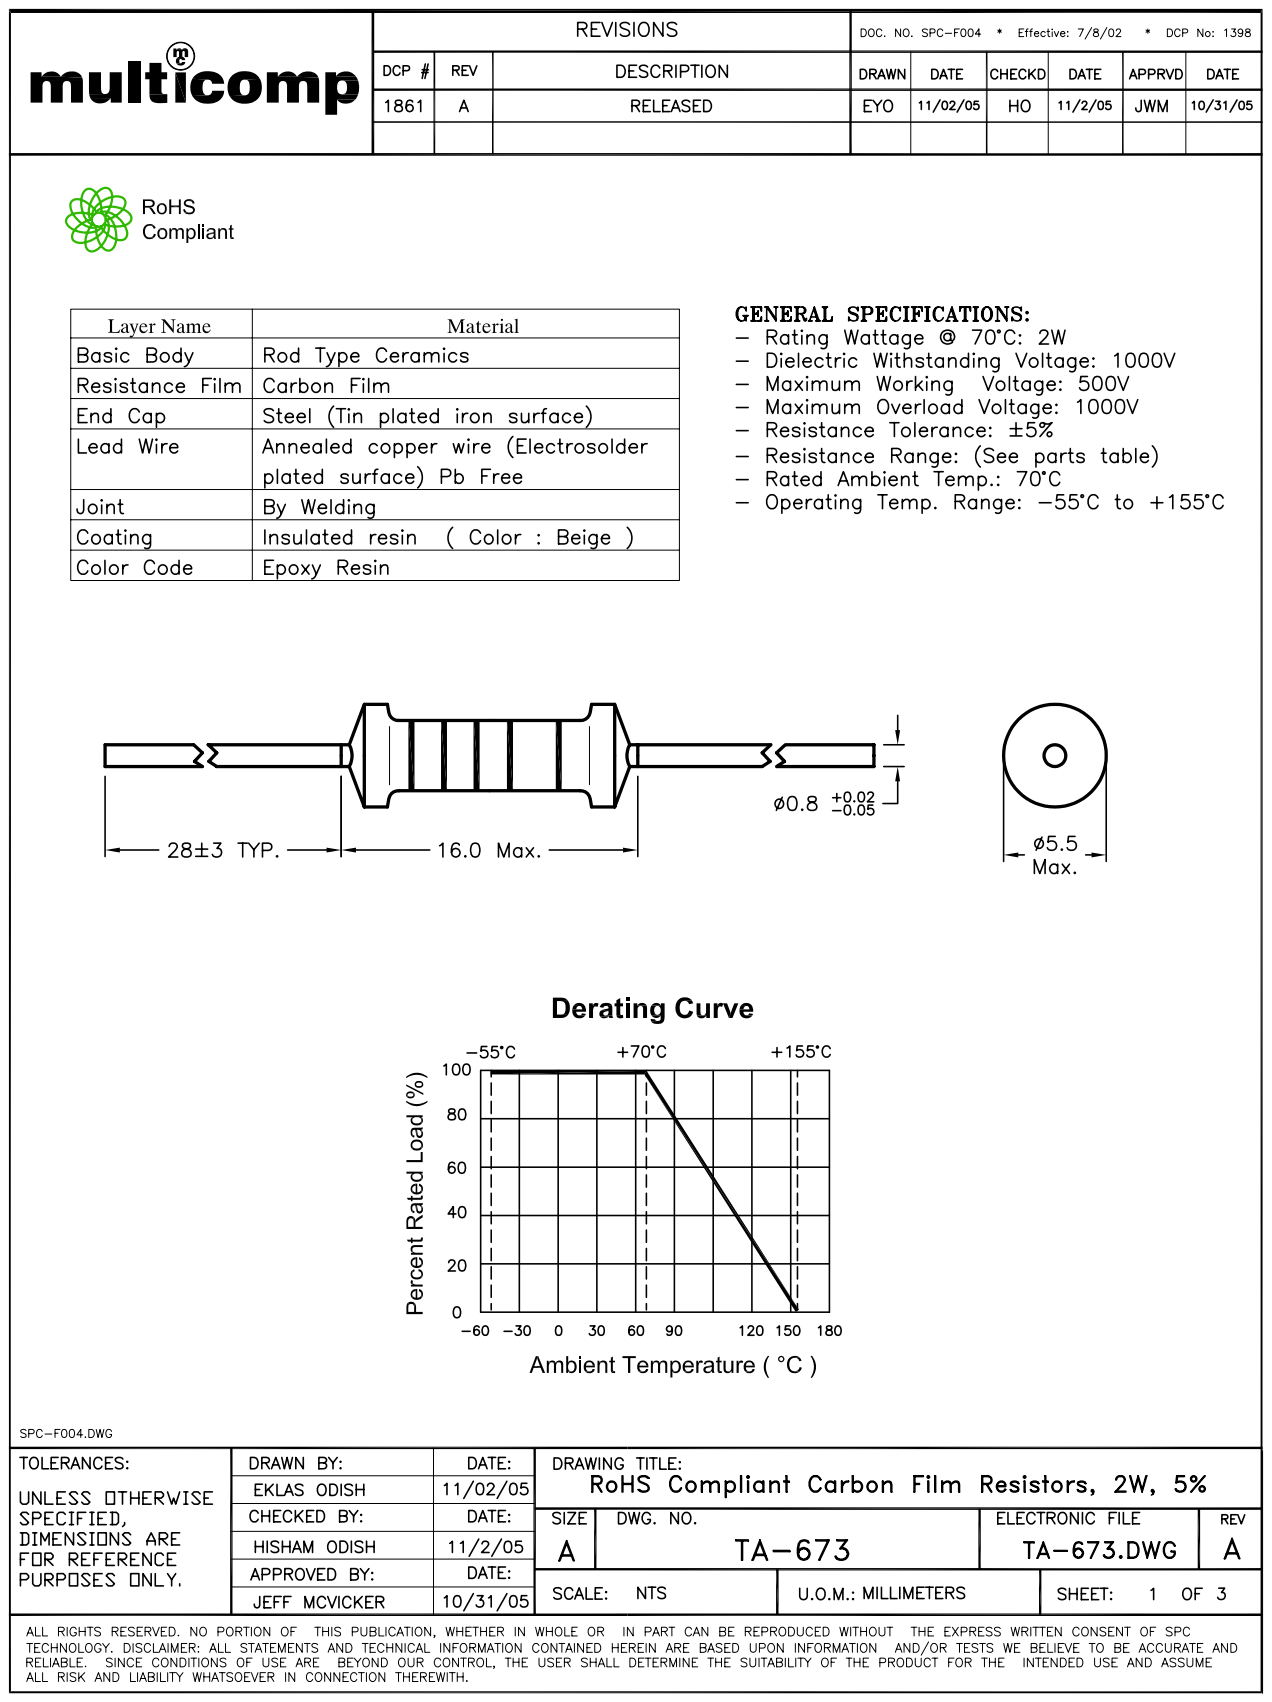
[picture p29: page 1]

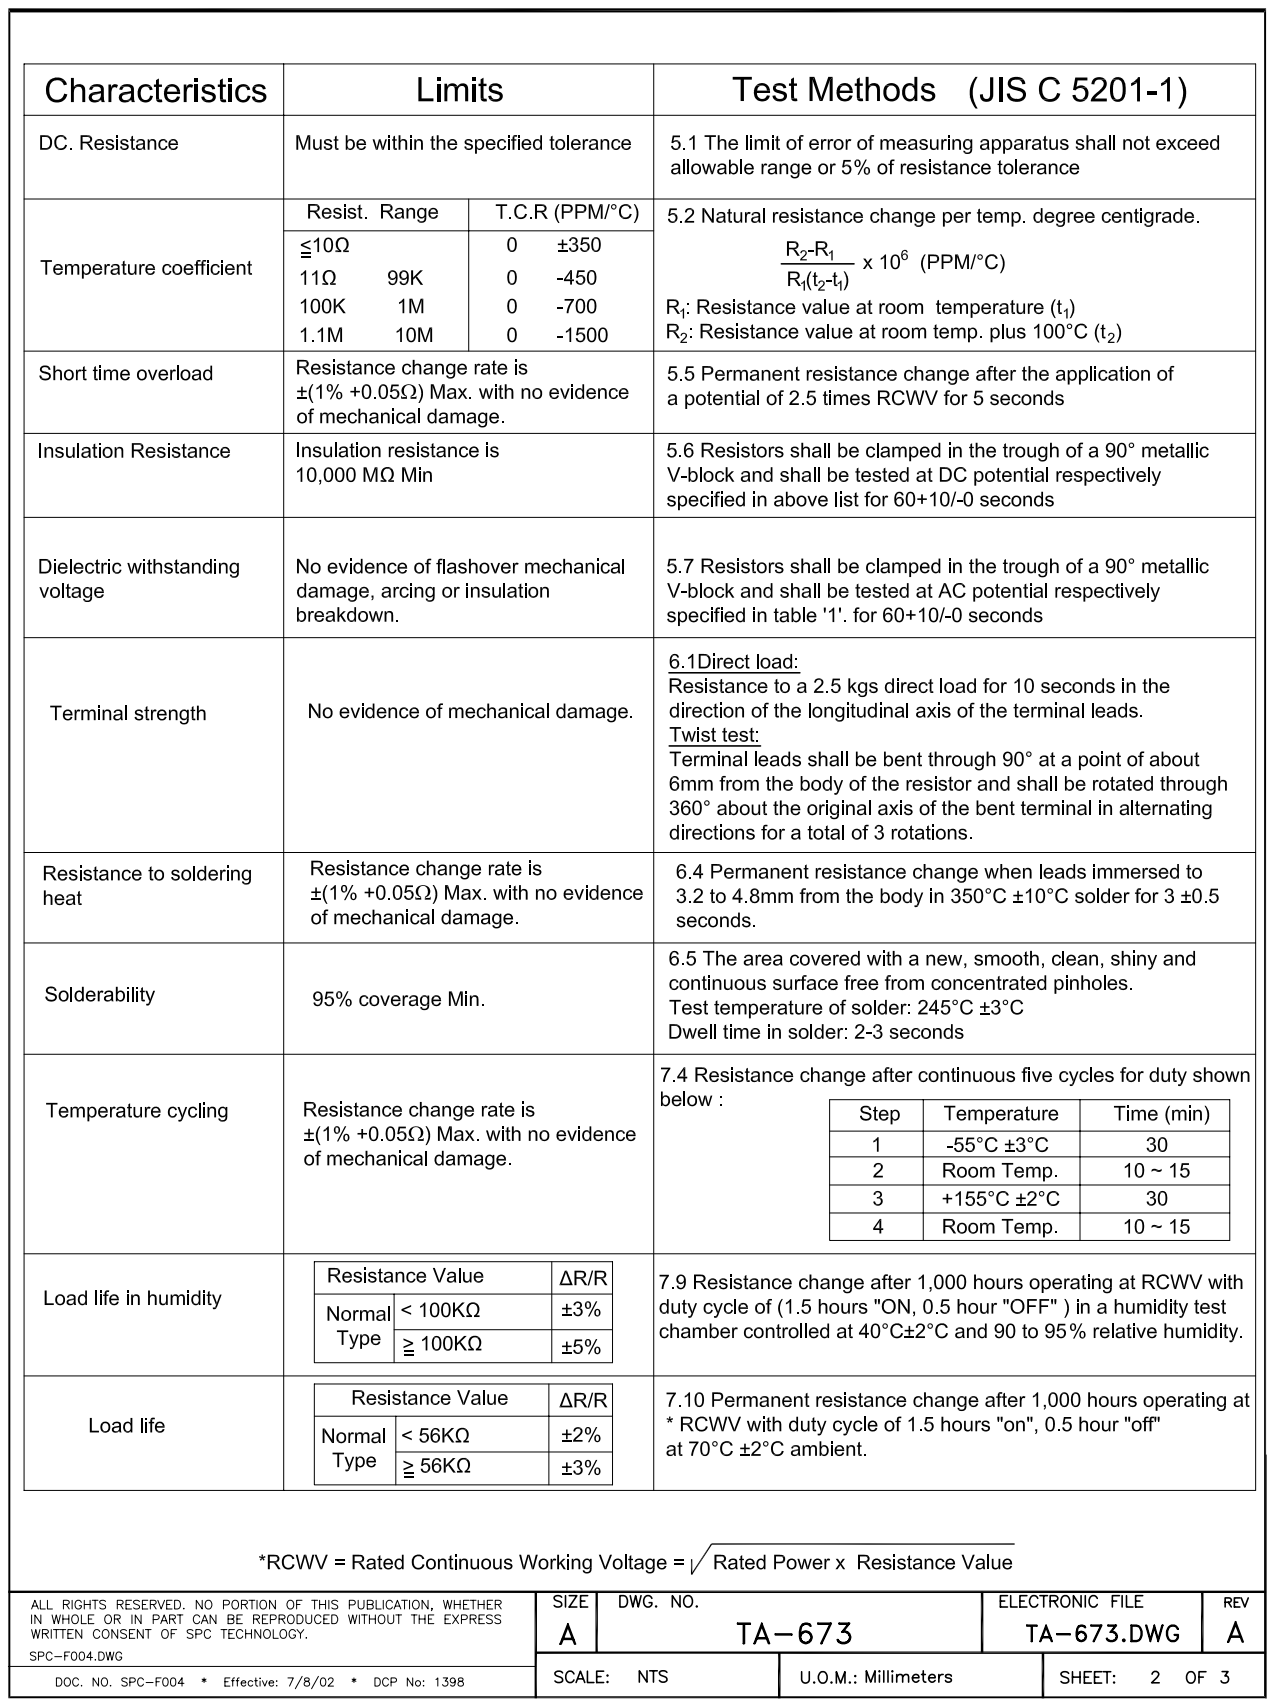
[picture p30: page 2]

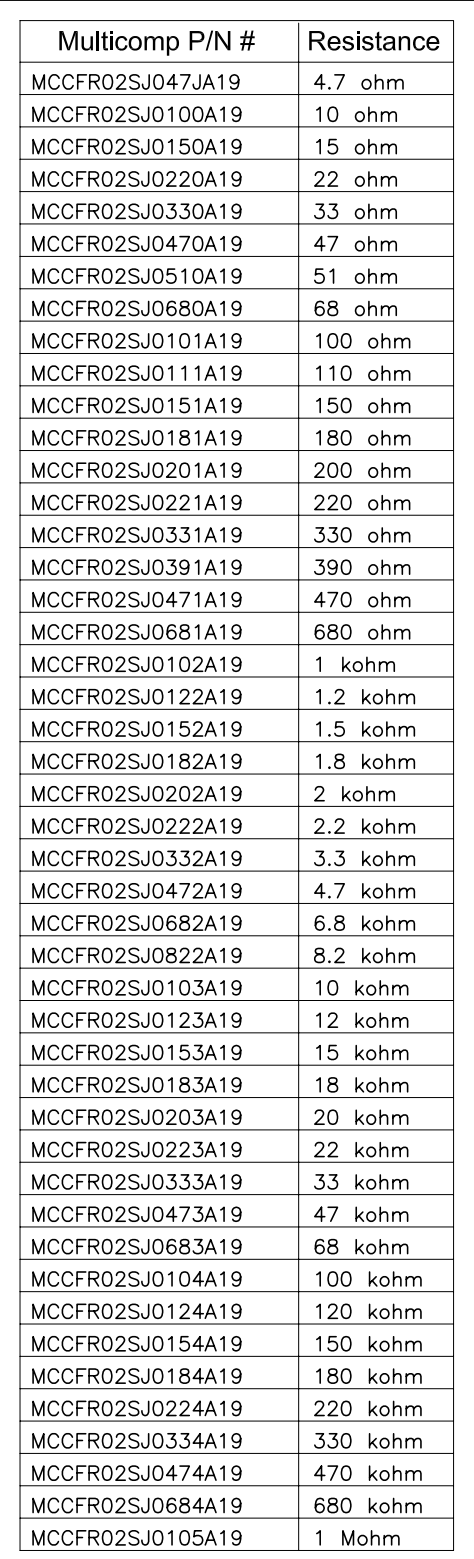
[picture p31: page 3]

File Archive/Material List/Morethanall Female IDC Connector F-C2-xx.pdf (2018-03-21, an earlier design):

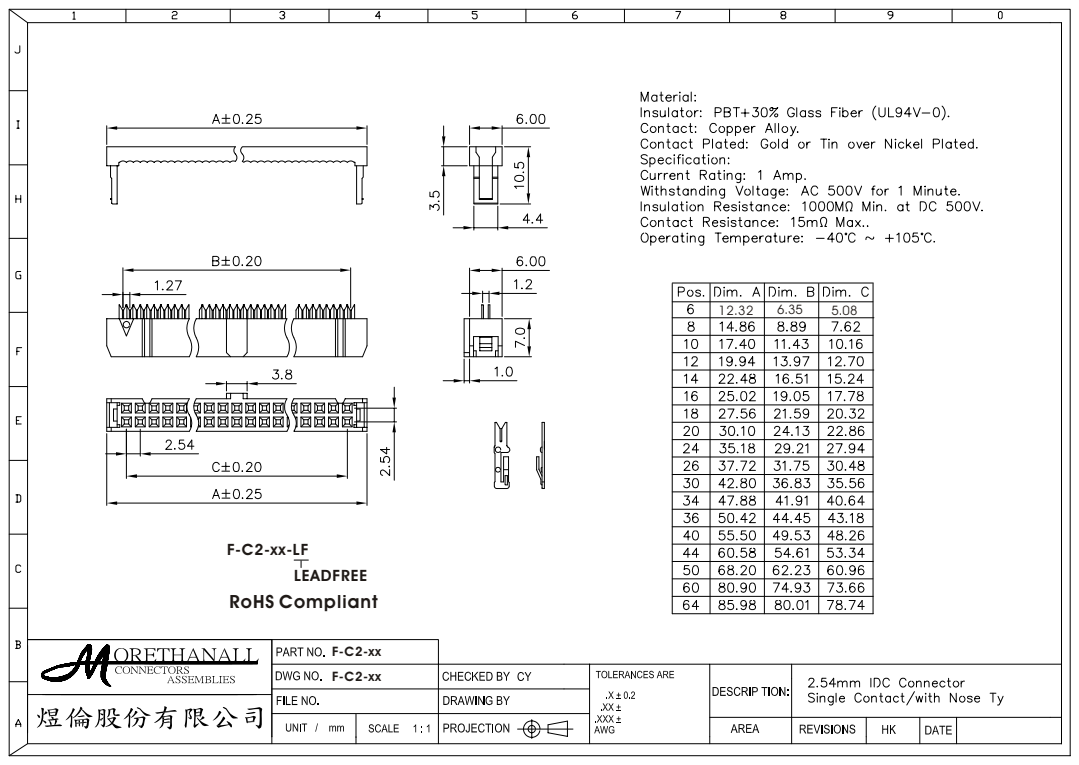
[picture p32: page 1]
LEADFREE RoHS Compliant

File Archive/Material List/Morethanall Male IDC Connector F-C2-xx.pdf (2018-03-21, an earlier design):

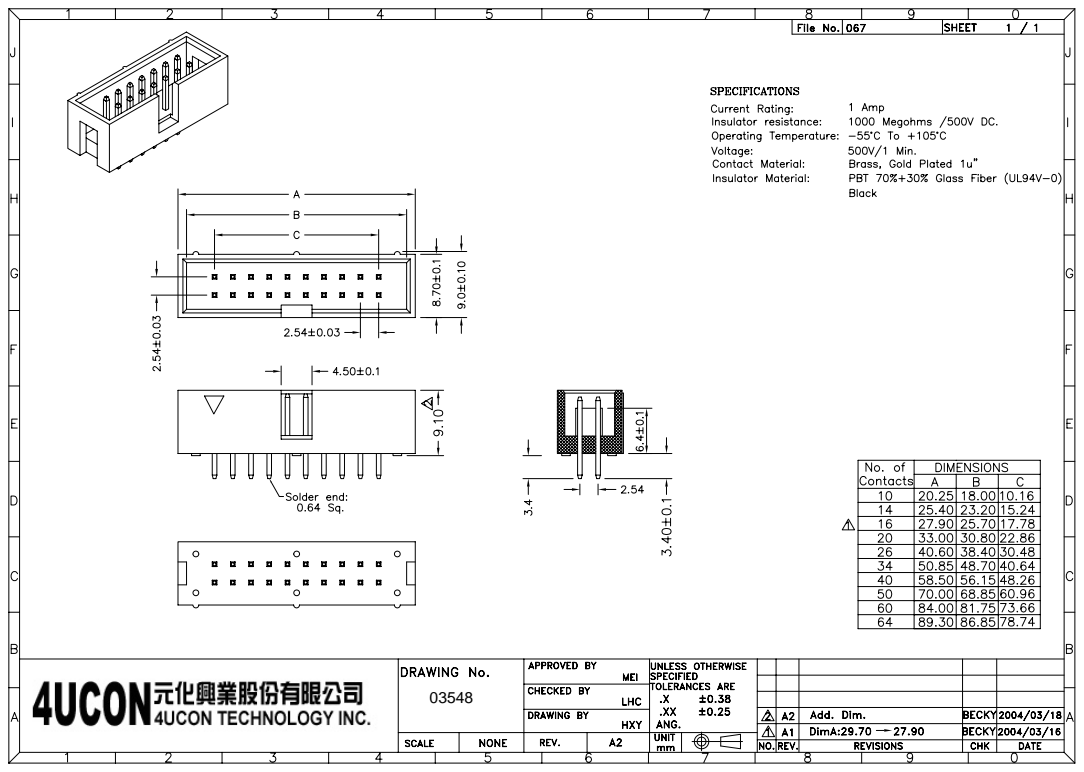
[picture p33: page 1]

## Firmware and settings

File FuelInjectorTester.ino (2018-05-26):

/* Fuel Injector Tester
 * NOTE: Possible pins to control fuel injector are 2, 3, 11, 12, and 13 (use these numbers in code)
 * These correspond to physical pins 3, 4, 5, 6 and 7 on the LCD Keypad Shield (respectively)
 */

#include <LiquidCrystal.h>
#include <pt.h>


/* Constants */
#define btnRIGHT  0
#define btnUP     1
#define btnDOWN   2
#define btnLEFT   3
#define btnSELECT 4
#define btnNONE   5
#define MAX_NUM_INJECTORS 6
#define POT_PIN 5
#define LARGE_RPM_INCREMENT 100
#define SMALL_RPM_INCREMENT 10
#define RPM_MAX 8000
#define RPM_MIN 0
#define DELAY_MIN 10
#define DELAY_MAX 15000
#define INJECTION_TIME_MAX 12
#define INJECTION_TIME_MIN 2
#define INJECTION_TIME_INCREMENT 1

/* Enums */
typedef enum _Mode
{
	DriveInjectors,
	DriveInjectorsAuto,
	DriveUI
} Mode;

/* Globals */

// Instantiate LCD panel struct with selected pins.
LiquidCrystal LCD(8, 9, 4, 5, 6, 7);

// Create array of pins to be used for fuel injectors.
// The order of the pins in this array matches the order of the LEDs on the board.
int INJECTOR_PINS[MAX_NUM_INJECTORS] = { 3, 13, 12, 2, 1, 11 };

// Firing order for four-cylinder engine.
int FOUR_CYLINDER_PINS[4] = { INJECTOR_PINS[0], INJECTOR_PINS[2], INJECTOR_PINS[3], INJECTOR_PINS[1] };

// Firing order for six-cylinder engine.
int SIX_CYLINDER_PINS[6] = { INJECTOR_PINS[0], INJECTOR_PINS[4], INJECTOR_PINS[2], INJECTOR_PINS[5], INJECTOR_PINS[1], INJECTOR_PINS[3] };

// Define some values used by the panel and buttons
int LcdKey = 0;
int AdcKey = 0;

// Protothread structures
static struct pt UiThread, DriverThread;

// Used to keep track of current RPM (set by user)
int CurrentRPM = 0;

// Used to keep track of current delay for fuel injectors (calculated from RPM)
int CurrentDelay = DELAY_MAX;

// Keep track of current firing order and number of cylinders.
int* CurrentFiringOrder = FOUR_CYLINDER_PINS;
int CurrentNumCylinders = 4;

// Keep track of current RPM tenth's place;
int CurrentRpmTenthsPlace = 0;

int CurrentInjectionTime = INJECTION_TIME_MIN;

// Mode of the application.
Mode CurrentMode = DriveUI;

/* Functions */

void setup()
{
	// Initialize the threads.
	PT_INIT(&UiThread);
	PT_INIT(&DriverThread);

	// Initialize all digital pins as an outputs for the fuel injector.
	int i;
	for (i = 0; i < MAX_NUM_INJECTORS; i++)
	{		
		pinMode(INJECTOR_PINS[i], OUTPUT);
	}

	// Start the library
	LCD.begin(16, 2);
	LCD.setCursor(0, 0);

    PrintMode();

	CalculateDelayAndRpmFromPot();

	// Move to the begining of the second line
	PrintConfigInfo(CurrentRPM, CurrentInjectionTime, CurrentNumCylinders);
}

void loop()
{
	ProcessUI(&UiThread);
	DriveFuelInjectorsPT(&DriverThread);
}

// Read the buttons
int ReadLCDButtons()
{
	AdcKey = analogRead(0);
									 
	if (AdcKey > 1000) return btnNONE;
	if (AdcKey < 50)   return btnRIGHT;
	if (AdcKey < 250)  return btnUP;
	if (AdcKey < 450)  return btnDOWN;
	if (AdcKey < 650)  return btnLEFT;
	if (AdcKey < 850)  return btnSELECT;

	return btnNONE;
}

int CalculateRpmFromPot(int pot, int tenthsPlace)
{
	int rpm = (int)(RPM_MIN + (RPM_MAX - RPM_MIN) * ((float)pot / 1024));
	rpm = (rpm / LARGE_RPM_INCREMENT) * LARGE_RPM_INCREMENT;
    rpm += tenthsPlace;
	return rpm;
}

int CalculateDelayFromRpm(int rpm)
{
	int delay = DELAY_MAX;
	if (rpm > 0)
	{
	    float period = 1000.0 / (rpm / 120.0);
		delay = (int)period - CurrentInjectionTime;
		if (delay < 0)
		{
			delay = DELAY_MIN;
		}
	}

	return delay;
}

int CalculatePotValue()
{
    int rawPotValue = analogRead(POT_PIN);
    return 1024 - rawPotValue;
}

void CalculateDelayAndRpmFromPot()
{
	// Read value of potentiometer.
	int potValue = CalculatePotValue();

	// Use potentiometer to set the RPM value.
	CurrentRPM = CalculateRpmFromPot(potValue, CurrentRpmTenthsPlace);

	// Recalculate burst delay based on the current RPM setting.
	CurrentDelay = CalculateDelayFromRpm(CurrentRPM);
}

void PrintToLine(char* data, int lineNumber)
{
    LCD.setCursor(0, lineNumber);

    char dataFormatted[17];
    sprintf(dataFormatted, "%-16s", data);

    LCD.print(dataFormatted);
}

void PrintConfigInfo(int rpm, int injectionTime, int numCylinders)
{	
	char rpmAndEngineString[17];
    sprintf(rpmAndEngineString, "%-4d%-4s%-2d%4d%-1s", rpm, "RPM", injectionTime, numCylinders, "C");
    sprintf(rpmAndEngineString, "%2s%-4d%4s%-2d%3s%1d", "R:", rpm, " IT:", injectionTime, " C:", numCylinders);

    PrintToLine(rpmAndEngineString, 1);
}

void PrintMode()
{
    if (DriveInjectors == CurrentMode)
    {
        PrintToLine("Running Test...", 0);
    }
    else
    {
        PrintToLine("Configure Test", 0);
    }
}

void ToggleMode()
{
	if (DriveInjectors == CurrentMode)
	{
		CurrentMode = DriveUI;
	}
	else
	{
		CurrentMode = DriveInjectors;
	}
}

void ToggleEngineType()
{
    if (4 == CurrentNumCylinders)
    {
        CurrentNumCylinders = 6;
        CurrentFiringOrder = SIX_CYLINDER_PINS;
    }
    else
    {
        CurrentNumCylinders = 4;
        CurrentFiringOrder = FOUR_CYLINDER_PINS;
    }
}

void UpdateRpmTenthsPlace(int delta)
{
    int updatedValue = CurrentRpmTenthsPlace + delta;

    if (updatedValue >= 0 && updatedValue <= 90)
    {
        CurrentRpmTenthsPlace = updatedValue;
    }
}

void UpdateInjectionTime(int delta)
{
    int updatedValue = CurrentInjectionTime + delta;

    if (updatedValue >= INJECTION_TIME_MIN && updatedValue <= INJECTION_TIME_MAX)
    {
        CurrentInjectionTime = updatedValue;
    }
}

// TODO: Separate button reading from LCD display logic. (should be separate threads)
static int ProcessUI(struct pt *pt)
{
	PT_BEGIN(pt);

	if (DriveUI == CurrentMode)
	{
		CalculateDelayAndRpmFromPot();
		PrintConfigInfo(CurrentRPM, CurrentInjectionTime, CurrentNumCylinders);
	}

	LcdKey = ReadLCDButtons();
	switch (LcdKey)
	{		
        case btnRIGHT:
		case btnLEFT:
		{
            if (DriveUI == CurrentMode)
            {
                ToggleEngineType();
                delay(500);
            }
			break;
		}
		case btnUP:
		{
            //UpdateRpmTenthsPlace(SMALL_RPM_INCREMENT);
            if (DriveUI == CurrentMode)
            {
                UpdateInjectionTime(INJECTION_TIME_INCREMENT);
                delay(500);
            }
			break;
		}
		case btnDOWN:
		{
            //UpdateRpmTenthsPlace(-SMALL_RPM_INCREMENT);
            if (DriveUI == CurrentMode)
            {
                UpdateInjectionTime(-INJECTION_TIME_INCREMENT);
                delay(500);
            }
			break;
		}
		case btnSELECT:
		{
			ToggleMode();
            PrintMode();
			
			delay(500);
			break;
		}
		case btnNONE:
		{
			break;
		}
	}

	PT_END(pt);
}

static int DriveFuelInjectorsPT(struct pt *pt)
{
	if ( (DriveInjectors == CurrentMode) && (CurrentRPM > 0))
	{
		static unsigned long timestamp = 0;
        static int i = 0;
        PT_BEGIN(pt);

		// Execute bursts of fuel injectors in proper order.
		for (i; i < CurrentNumCylinders; i++)
		{
			digitalWrite(CurrentFiringOrder[i], HIGH);
			delay(CurrentInjectionTime);
			digitalWrite(CurrentFiringOrder[i], LOW);

            PT_WAIT_UNTIL(pt, millis() - timestamp > (CurrentDelay / CurrentNumCylinders));
            timestamp = millis();
		}
        i = 0;

		PT_END(pt);
	}
}

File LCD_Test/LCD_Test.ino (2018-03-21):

//Sample using LiquidCrystal library
#include <LiquidCrystal.h>

/*******************************************************

This program will test the LCD panel and the buttons
Mark Bramwell, July 2010

********************************************************/

// select the pins used on the LCD panel
LiquidCrystal lcd(8, 9, 4, 5, 6, 7);

// define some values used by the panel and buttons
int lcd_key     = 0;
int adc_key_in  = 0;
#define btnRIGHT  0
#define btnUP     1
#define btnDOWN   2
#define btnLEFT   3
#define btnSELECT 4
#define btnNONE   5

// read the buttons
int read_LCD_buttons()
{
 adc_key_in = analogRead(0);      // read the value from the sensor 
 // my buttons when read are centered at these valies: 0, 144, 329, 504, 741
 // we add approx 50 to those values and check to see if we are close
 if (adc_key_in > 1000) return btnNONE; // We make this the 1st option for speed reasons since it will be the most likely result
 // For V1.1 us this threshold
 if (adc_key_in < 50)   return btnRIGHT;  
 if (adc_key_in < 250)  return btnUP; 
 if (adc_key_in < 450)  return btnDOWN; 
 if (adc_key_in < 650)  return btnLEFT; 
 if (adc_key_in < 850)  return btnSELECT;  

 // For V1.0 comment the other threshold and use the one below:
/*
 if (adc_key_in < 50)   return btnRIGHT;  
 if (adc_key_in < 195)  return btnUP; 
 if (adc_key_in < 380)  return btnDOWN; 
 if (adc_key_in < 555)  return btnLEFT; 
 if (adc_key_in < 790)  return btnSELECT;   
*/


 return btnNONE;  // when all others fail, return this...
}

void setup()
{
 lcd.begin(16, 2);              // start the library
 lcd.setCursor(0,0);
 lcd.print("Push the buttons"); // print a simple message
}
 
void loop()
{
 lcd.setCursor(9,1);            // move cursor to second line "1" and 9 spaces over
 lcd.print(millis()/1000);      // display seconds elapsed since power-up


 lcd.setCursor(0,1);            // move to the begining of the second line
 lcd_key = read_LCD_buttons();  // read the buttons

 switch (lcd_key)               // depending on which button was pushed, we perform an action
 {
   case btnRIGHT:
     {
     lcd.print("RIGHT ");
     break;
     }
   case btnLEFT:
     {
     lcd.print("LEFT   ");
     break;
     }
   case btnUP:
     {
     lcd.print("UP    ");
     break;
     }
   case btnDOWN:
     {
     lcd.print("DOWN  ");
     break;
     }
   case btnSELECT:
     {
     lcd.print("SELECT");
     break;
     }
     case btnNONE:
     {
     lcd.print("NONE  ");
     break;
     }
 }

}

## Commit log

2018-03-21 Initial commit.
    [LCD Pinout.xlsx, fuel injectorREVB.brd, fuel injectorREVB.sch]
2018-03-22 Recolored connections to make solder bridges more clear.
2018-03-23 Repositioned transistors for better 6-injector layout (minimizing change of overheating) - Created lines for solder bridges (the 'bottom-copper' lines)
2018-03-24 Added resistors to LEDS
2018-04-02 Added cables for LEDs and Digital I/O pins to circuit diagram - Created plan for soldering prototype board.
2018-04-03 Re-wired the ground connections for LEDs - The long ground solder-bridge would not work because it would be exposed on the top-side of the board (potentially shorting the LEDs)
2018-04-10 Move power connections for fuel injector cables.
2018-05-03 Updated wire descriptions for fuel injector power wires.
2018-05-05 Fixed design to reflect change that was made during solder-bridging process.
2018-05-25 - Determine which pins match which LEDs - The output signals are now distributed evenly throughout the timespan of CurrentDelay.
2018-05-25 Issue #3: Made number of cylinders (4 or 6) configurable.
    [FuelInjectorTester.ino]
